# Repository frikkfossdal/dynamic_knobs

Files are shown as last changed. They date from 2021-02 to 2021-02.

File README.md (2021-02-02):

# Haptic Knob Interface

**NOTE Documentation is currently havoc. I will return in future for cleanup.**
 
I want to have knobs that uses torque and position control to provide a diverse and muli-purpose interface. Essentially I want to be able to modulate torque based on selected application. Random Access Project gives a good summary in [this](https://www.youtube.com/watch?v=9Eh1p_rUQMA) video. I think interfaces like this also holds potential for machine control. I'm imagining an interface that could enable users to feel / interact in more tangible ways by reflecting stock or machine properties through torque. More reflections about this later. I want to implement!

I have aquired some key ingrediences to get me started. I won't explain the details behind BLDC control and FOC, but here is a list of useful links and resources:

- [Jake's notes on BLDC drivers](https://gitlab.cba.mit.edu/jakeread/atkbldcdriver/-/tree/master/education)
- [Great Scott](https://www.youtube.com/watch?v=Nhy6g9wGHow&feature=emb_logo)
- [Trinamic: look to datasheet](https://www.trinamic.com/products/integrated-circuits/details/tmc4671/)
- [Book: Electric Motors And Drives](https://www.sciencedirect.com/book/9780080983325/electric-motors-and-drives)

I'm thinking that my knobs will not require a lot of torque and current. so I dont really need a superpowerful driver; for first round of implementation I will have a go with the [L6234](https://www.st.com/resource/en/datasheet/cd00000046.pdf) which should give me up to 5Amps to make my coils move. These are nicely baked into the [simpleFOC](https://simplefoc.com/#simplefoc_shiled). As I get comfortable I might come back to this point and readjust course by making a more customized circuit board.

## Log

# 01022021

Made good progress on both parts assembly and testing of initial prototype. At this point in time I have a working prototype of the setup; I have a working implementation of FOC on a knob that consist of 3D printed parts. But it is a rough build centered around a 3D printed shaft. For my next move I want to incorporate some real parts; a precission steel shaft with bearing for support and a polulu mounting hub. This should improve the knob feeling I'm longing for drastically. I've put together a parts list with supplier [here](https://docs.google.com/spreadsheets/d/1L6t7pLEjz3Pts3YDK6dYrAYIaIHmlakXx8iCuhCMrLw/edit?usp=sharing).

I've updated the CAD model of the knob assembly to fit this new pattern. I will document this in more detail in future. Here is a quick screenshot from fusion:

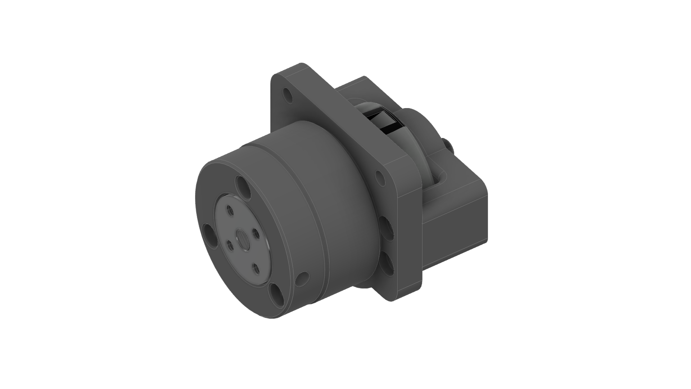
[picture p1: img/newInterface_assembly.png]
new knob assembly

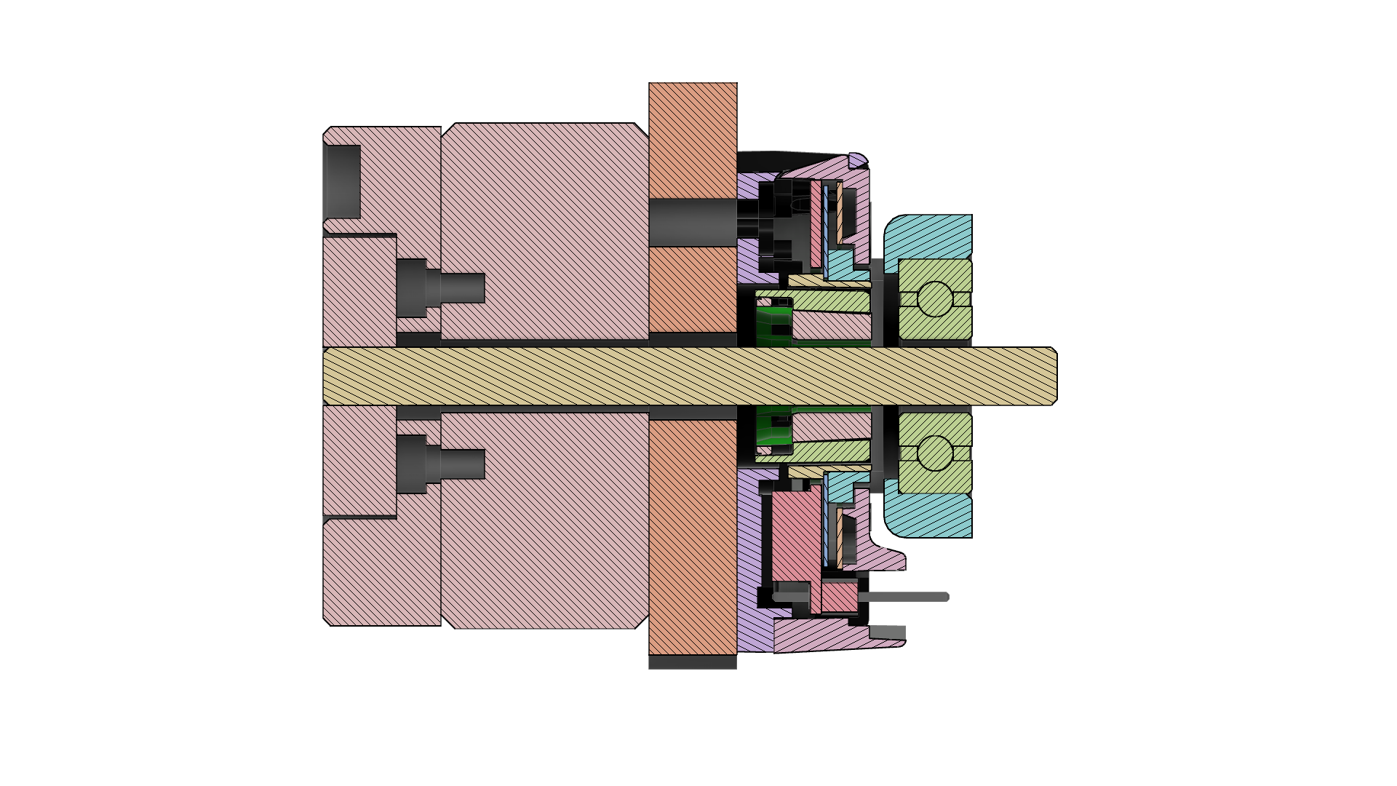
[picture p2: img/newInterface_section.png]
new knob assembly section


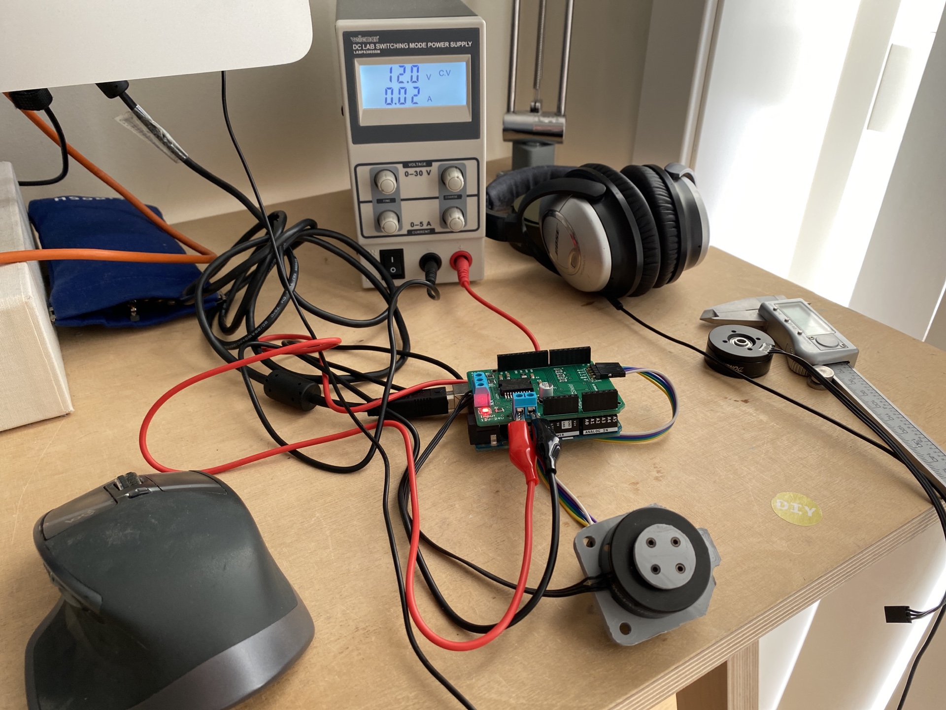
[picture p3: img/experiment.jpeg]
experiment setup


As for testing results I'm including some plots of the knobs dynamics. Here is a plot of me setting knob angle in software. Red line is angle from encoder and gray line is knob rotational velocity.

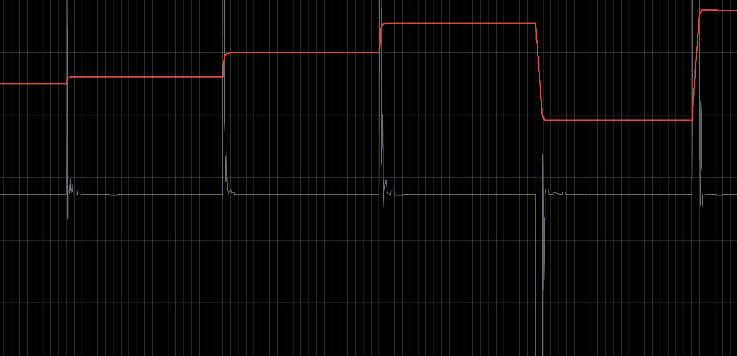
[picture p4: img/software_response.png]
software reference points


and here is a plot of me interacting with the knob:

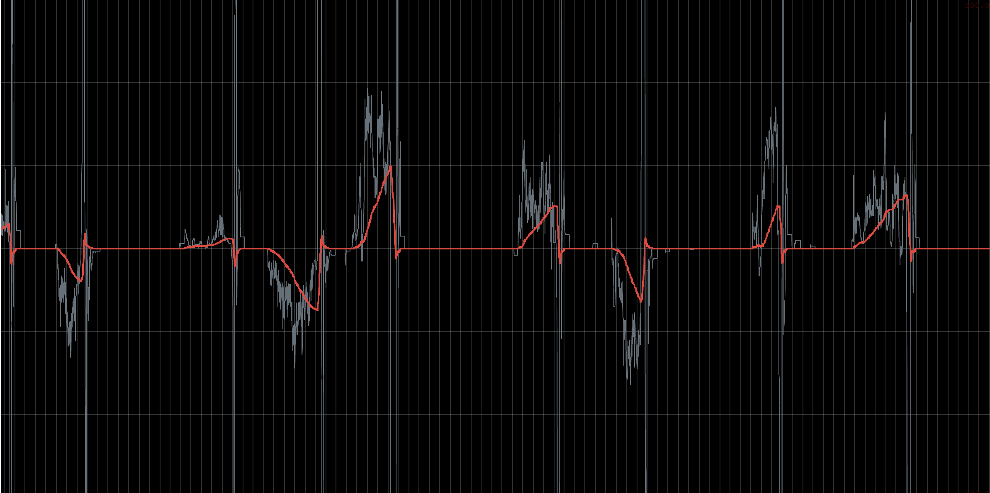
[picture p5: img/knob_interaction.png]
knob interaction


There is a small amount of overshoot, which I think is not a big problem at this point. I will circle around and spend more time on tuning once I have proper mechanics implemented.

Next step will be to print new parts and wait for shaft and mounting hub. Excitement!

# 25012021

Time is short. I've figured out where I want to go with this. This thing will be heavily inspired by teenage engineering's [ortho remote](https://teenage.engineering/products/orthoremote), but with the addition of dynamic torque / haptics. I'll come back with a more serious mockup of the direction in very near future.

As for the embedded / hardware prototype I have a couple of main notes. I think I want to use a ~~SAMD21~~ SAMD5x microcontroller family together with a L6234 to make this thing move. I have a couple of things I need to figure out before I advance on any serious desigs. As of now these things are:

- use simpleFOC to explore L6234
- use MKR1010 to explore SAMD21
- figure out a setup where these are powered by a LiPo battery (thing I need a boost converter to do this)

# 26122020

First jab on a prototype. I'm using an AMT103 capasative encoder which is a shaft-encoder, so I need to figure out a way to make this work with my hollow shaft motor. As a first instance I'm content with a 3D printed shaft to make this work. I can return to this point in the future. With this out of the way, the rest of the design should be fairly easy to put together. I'm aiming for a 3D printed instance of this that I can use for testing. I will think more about casing and detailing layout later. Some Nils Frahm and Fusioning gave me this:

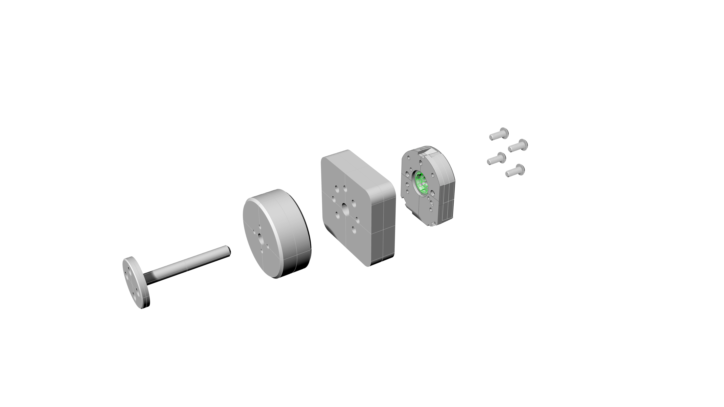
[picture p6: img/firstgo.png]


# 31122020

I need to start keeping track on offsets that I use in 3D print design. Too much time has been wasted. I've started a sheet where I keep track of this [here](https://docs.google.com/spreadsheets/d/1FFUu7XrTB8tco7_t6ya7o5u4sKuB1yexN5Hv9sAugUY/edit#gid=0).

Also, it seems like my hacky 3D printed encoder-shaft needs to be 3D printed slooow for accuracy. Current settings 40mm/s with 0.1 layer height.

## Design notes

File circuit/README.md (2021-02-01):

# Dev log for haptic circuit

This is my first round of designing circuitry using PCB software AND(!) ordering a pcb from a vendor. Excitement is very high! Since I have a SAMD21 at hand (Arduino MKR1010) I will use this as the basis of my circuit. The gimbal motors I will be using to actuate things should not require too much heavy lifting, so for pushing current into the coils I will be using the L6234. I also need to figure out some kind of encoder connection. So, summary design requirements:

- SAMD21 circuitry (usb connections, bootloader upload, power, indicators)
- L6234 circuitry
- Encoder connections.

For design I will be using the Eagle integration in Fusion360. For best practice circuit design (my electronic design skills are weak) I will use [SparkFun](https://cdn.sparkfun.com/assets/4/4/f/2/a/Qwiic_Pro_Micro_V2_0_USB_C_Schematic.pdf) schematics (just pick any board that is remotely close to what you are doing and study schematics). A lot of the circuit "modules" are repetative (e.g voltage regulators, JTAG for bootloading, USB for coms, etc).

I will also attempt to use JLPCBs SMT assembly service, so componentes need to match their inventory (which seems to be quite abundant).

These are highlights of what I need to figure out:

- How to bootload? I think both CBA and Sparkfun has some good documentation about this. More will follow
- How to control voltage? Sparkfun has alot of examples.

# 29012021

Yesterdays adventure sent me into a world good ol' fashion control theory engineering. I have returned to the domain of signal processing and tuning PID controllers. Lucky me I have a diploma lying around somewhere in this domain. Unlucky me I didn't really understand much of this when I was learning it, and I didn't really have a practical "hanger" to secure the knowledge I was exposed to. Well, now I'm back and I am hungry to understand.

My knob interface requires a fast and stable system in order to feel good. At the end of the day, this is a human interaction so we don't need to move in light speed, but the circuit driving the interaction needs to be fast and snappy in order to make the magnetic field turning / resisting the knob feel good. I also have the impression that if the controller PWMing the magnetic field is blazing fast, I will get rid of the field humming that I am currently experiencing using the Arduino Mega (which is really the atMega328 clocking away at 16Mhz). The SAMD2x series has a clock speed of 48Mhz, which should make the PWMing much smoother. However, I now see that the SAMD5x series has a clock speed of 120Mhz. Further thoughts are needed on this point. Im noting this as a **return in the future**. Some numbers to work on:

`I can hear 20kHz`

`I can see roughly 50Hz`

`ATmega328 clock speed 16Mhz`

`ATSAMD2x clock speed 48Mhz`

`ATSAMD5x clock speed 120Mhz`

`Human hearing is between 20 - 20k Hz`

For now, I think I shouldn't worry too much about sampling rate in terms of me perceiving the response on a screen. A general thought I have is that I want to be able to view the data from the system in browser. This means having some kind of server receiving data over serial port and pushing the data into the browser over web sockets (TCP), which should cause some delay in terms of real-time monitoring. I think this delay is not really a problem. For now, I will stick to this architecture and see where it takes me, and learn about these problems as I go along. Here we go.

General plan going into this. Express server based on node.js has to do three things:

- Read serial data
- Host web-client that includes charts.
- Host web socket server that pushes data into web-client

I will be using [smoothie charts](http://smoothiecharts.org) for visualization and socket.io for web sockets. Smoothie has a wonderful tool for pre-designing charts [here](http://smoothiecharts.org/builder/).

Implementation is semi-successful. I am parsing serial data on server side, and I am sending it to browser. On client side I am running smoothie charts. I need to spend more time on parsing before I send over socket. Out of time now. For now I will end on a chart full of random data points sent over socket.

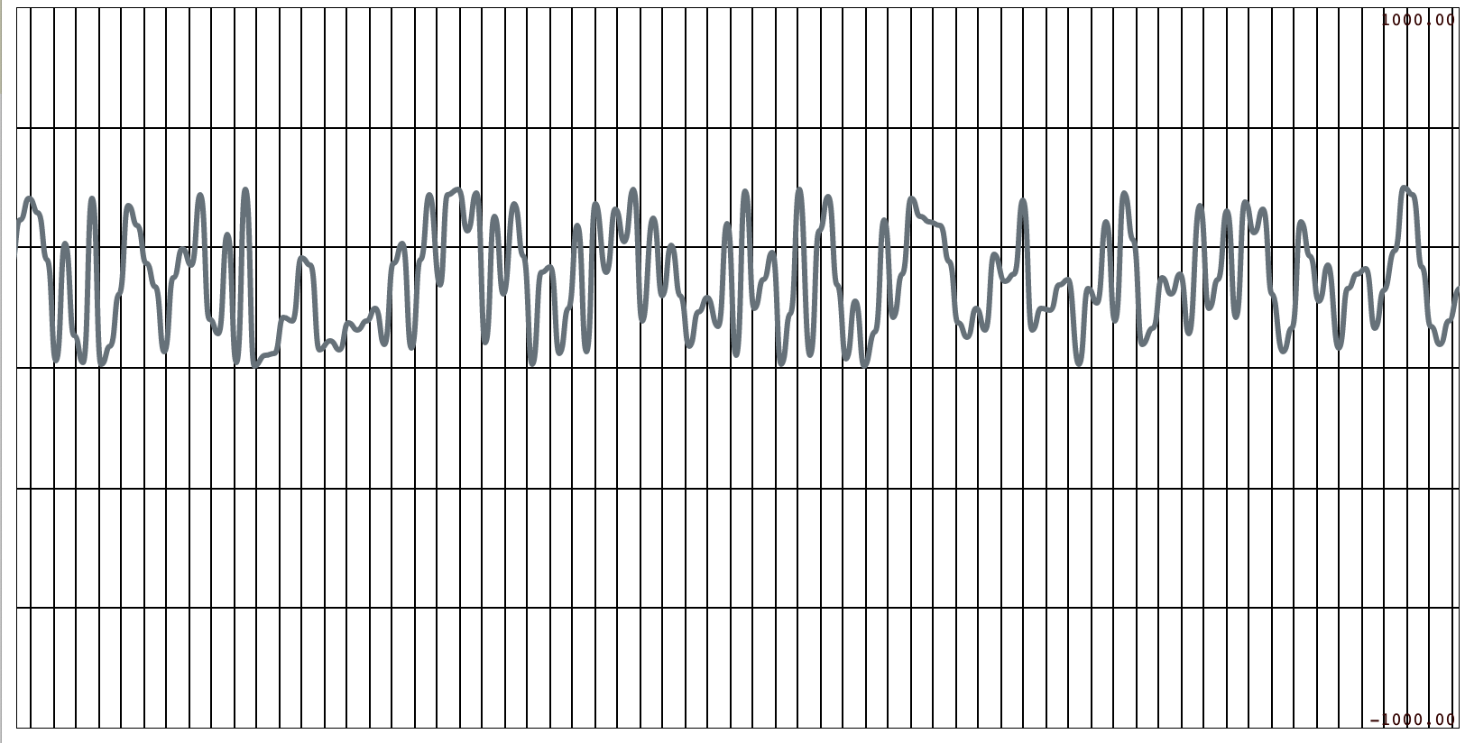
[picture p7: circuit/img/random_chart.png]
random data points in time


Will try to return later today and fix this.

# 28012021

I've made a working prototype of the circuit using the SimpleFOCshield and a Arduino UNO (I know, its not the SAMD21, but we'll return to that in a moment). The setup I'm using is fairly well documented on SimpleFOC site. In short, cheap gimbal motor from [Ebay](https://www.ebay.com/itm/BGM2804-Brushless-Gimbal-Motor-Hollow-Shaft-for-Camera-Mount-FPV/172292079620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), [CUI AMT103](https://www.digikey.com/en/products/detail/cui-devices/AMT103-V/827016) encoder, SimpleFOC shield on a Arduino UNO connected to a 12V PSU.

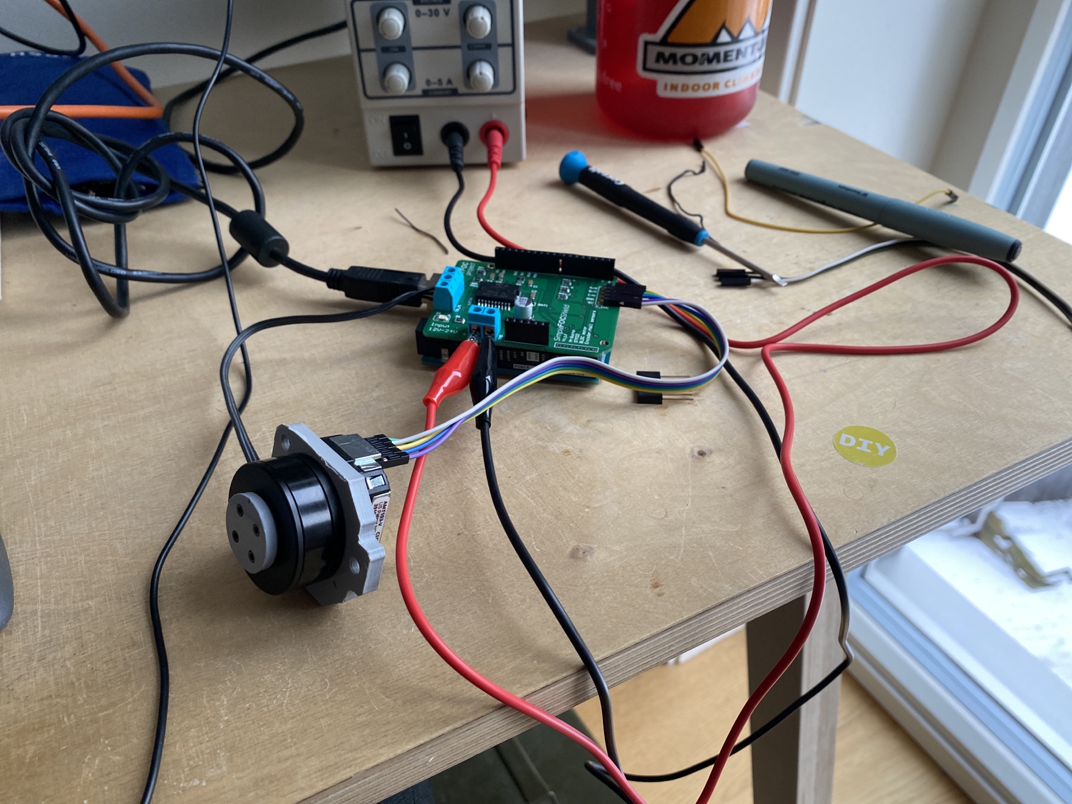
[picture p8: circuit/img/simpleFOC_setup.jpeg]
setup


This is a much better starting ground, and I feel more confident at the moment. I have a working closed loop position program. The PID controller in the FOC algorithm comes with default parameters that feels kind of slow and not snaggy as I imagined. I need to spend some time here to get the right feel. Next thing on the todo-list is to visualise set-point vs response and start tuning. Exciting! Some parameters so I don't repeat myself:

Motor:
`BLDCMotor motor = BLDCMotor(9, 10, 11, 7, 8);`

Encoder:
`Encoder encoder = Encoder(2, 3, 2048);`

Slow but staple PI (D) controller:

`motor.PID_velocity.P = 0.2;`

`motor.PID_velocity.I = 63;`

`motor.PID_velocity.D = 0;`

I'll leave this for now and return with plots in near future.

# 27012021

Ok. I've done some research and I have a rough idea of what I want to do.

First, battery circuit: I want to use [this](https://www.sparkfun.com/products/15217) piece from Sparkfun to do charging. I've checked JLCPCB and they have the [MCP73833](https://jlcpcb.com/parts/componentSearch?searchTxt=MCP73833) chip it uses. STOP: before I choose this, I have to settle on what kind of battery I want to use - normal LiPo might not be the answer since we ideale want semi high voltage for the motor. [Sparkfun](https://learn.sparkfun.com/tutorials/battery-technologies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) has a good guide on picking batteries here.

_time goes by_

I have to do more research here. It might be a good idea to separate motor control from battery circuit. Question to ponder here; can I run the motor on 5V? In that case I can piggyback on the [Adafruit PowerBoost](https://www.adafruit.com/product/2465) design. Next step on this point will be to do some lab testing with the L6234 and the motor I have at hand. God I want this to work. Update: No good. It looks like most gimbal motors require 3-4s Lipo packs, which makes sense; there are a lot of windings and it will require a decent amount of pushing force to push current through the windings. Ok. Back to the drawing board. I found a new search phrase that might be useful: BMS circuits. Have a look at [this](https://electronics.stackexchange.com/questions/317019/diy-18650-4s-battery-pack-how-to-charge-how-to-build) thread.

I'm considering just skipping this part for now, and just have the projects either use AA batteries, or just connect to power source.

Moving on. I think that the SAMD21 chip has internal pull-ups that I can use, so for now I will not worry about this. I'm noting this as a point to come back to before I order the design. Also, SAMD21-vise, there is a lot of good reference designs to follow; CBA, Adafruit and Sparkfun. As for now, I will follow intuition, and then use one of these to verify myself.

I found several good references on how to design the circuit around the L6234 chip. The best one so far (maybe not a big surprise) is the one in the data sheet. But references are always good!

# 26012021

Started on schematics. Learned tons about Fusion360 electronics design. It's quite neat actually. There are already tons of components and libraries available through [Library.io](library.io). I added SAMD21 QFN32 package to the library following [this tutorial](https://www.youtube.com/watch?v=zqar0XWtFaY).

So far I think I've figured out voltage regulator for the controller, but I have to study it a bit more to understand it. I think I saw a guide on best practice on Sparkfun at some point. Also conflicted about whether I should choose USB type B or the future Type C. I also need to figure out how this whole bootloader uploading business works. I think cba/Jake has some guide [documentation on this](https://gitlab.cba.mit.edu/jakeread/arm-target-programming).

More on this next time. As for now, I will consider this a good start.
2

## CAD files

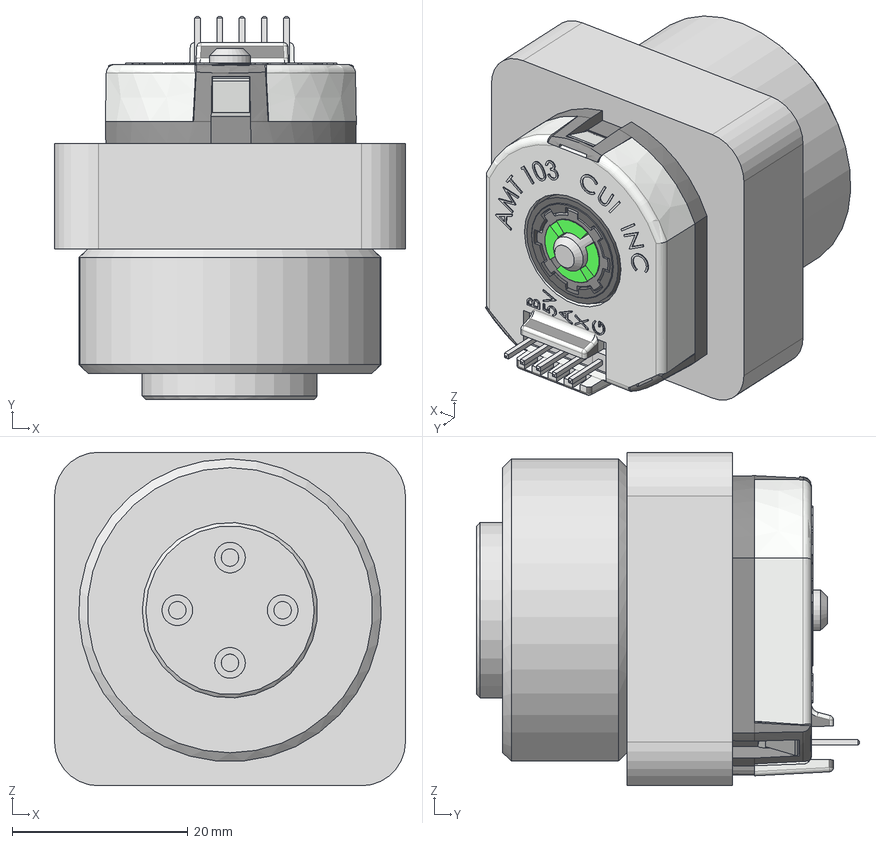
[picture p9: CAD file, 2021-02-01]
cad/newInterface v1.step
40.0 x 43.7 x 38.0 mm
ipower?
AMT-Sleeve-REV-D_5 mm
AMT-Hub-Top-REV-D1
AMT-Hub-Bottom-REV-B
AMT10X-Shaft-Adaptor-REV-E
Receiver-board
Rotor-board-REV F
Transmitter-board AMT10_AMT-103
AMT-103-Base-REV-K
AMT-103-Top-Cover-REV-H
92095A181 x 4

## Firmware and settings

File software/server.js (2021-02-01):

const express = require("express");
const chalk = require("chalk");
const log = console.log;

var SerialPort = require("serialport");
const Readline = require("@serialport/parser-readline");

var sp = new SerialPort("/dev/tty.usbmodem14601", {
  baudRate: 115200,
});

var parser = new Readline();
sp.pipe(parser);

//this needs to be refined
parser.on("data", (line) => {
  let data = line.split(",");
  console.log(data[0] * (180 / Math.PI) + " " + data[1] * (180 / Math.PI));
  io.sockets.emit("message", data);
});

// setInterval(() => {
//   let rndAngle = Math.random() * 10;
//   sp.write(rndAngle + "\n");
// }, 5000);

let app = express();
const port = 8080;

var server = app.listen(port, () => {
  log("listening on port: " + port);
});

app.use(express.static("client", (hello) => {}));

var io = require("socket.io")(server);
io.on("connection", (socket) => {
  log(chalk.white(socket.id + " connected "));

  // setInterval(() => {
  //   socket.emit("message", Math.random() * 5);
  // }, 100);
});

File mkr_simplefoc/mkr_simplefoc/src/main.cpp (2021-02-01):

/**
 *  Encoder example code 
 * 
 * This is a code intended to test the encoder connections and to demonstrate the encoder setup.
 * 
 */

#include <SimpleFOC.h>


Encoder encoder = Encoder(2, 3, 2048,4);
// interrupt routine intialisation
void doA(){encoder.handleA();}
void doB(){encoder.handleB();}

void setup() {
  // monitoring port
  Serial.begin(115200);

  // enable/disable quadrature mode
  encoder.quadrature = Quadrature::ON;

  // check if you need internal pullups
  encoder.pullup = Pullup::EXTERN;
  
  // initialise encoder hardware
  encoder.init();
  // hardware interrupt enable
  encoder.enableInterrupts(doA, doB);

  Serial.println("Encoder ready");
  _delay(1000);
}

void loop() {
  // display the angle and the angular velocity to the terminal
  Serial.print(encoder.getAngle());
  Serial.print("\t");
  Serial.println(encoder.getVelocity());
}

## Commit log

2021-02-01 First push
    [newInterface v1.step]
2021-02-01 fixed new shaft and mounting hub
